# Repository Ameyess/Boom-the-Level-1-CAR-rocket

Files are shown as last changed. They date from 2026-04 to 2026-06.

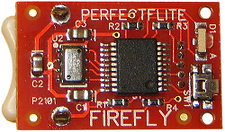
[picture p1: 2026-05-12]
Firefly/Firefly.png

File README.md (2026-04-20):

# Boom-the-Level-1-CAR-rocket
This is Boom (my level 1 certification rocket)

Boom is a single-stage Level 1 high-power rocket designed and built from scratch for CAR L1 certification. It features a 3D-printed nose cone, CNC-machined trapezoidal fins and a PerfectFlight Firefly altimeter for apogee detection as well as ejection charge deployment.

# Why I Built This
I've been fascinated by space and rockets since I was 10... playing games like Universe Sandbox and dreaming about what's out there beyond Earth. I loved learning how propulsion systems and aerodynamics work, seeing how to make things glide more smoothly through the air and how air can be a little funky. Since I was 10, I've been keeping up with this YouTuber called Integza and he really brought me into the world of rockets and propulsion. On top of all this I want to pursue a career in aerospace engineering. Instead of building a wind tunnel or a similar project, I wanted to get my L1 certification. I wanted to actually build something real before entering the field. Boom is that project: a fully designed, simulated, and flown (hopefully) rocket that I can point to and say I made it.

# Project images

## OpenRocket Design


## FULL CAD MODEL


## Nose Cone


## Body tube


## Fins


## Payload


## Link to Onshape
https://cad.onshape.com/documents/796e5f2c6edbdd94a10a7fd9/w/921c18dcc929cb2f28ee7e6d/e/6b2fc36c223bcd20e07954f4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

# Simulated Flight Performance 
To perform the simulations, I used OpenRocket. I first designed the whole rocket in OpenRocket then moved it to CAD for it to be fully 3D modelled and ready to construct. Simulations were run using the HP-H195NT-10 motor.

| Parameter | Value |
| --- | --- |
| Projected Apogee | 1484m | 
| Max Velocity | 470 m/s |
| Stability Margin| 1.8 Cal |
|Recovery | Parachute deployed at apogee|

# Design Overview
## Airframe
- Nose cone: 3D printed in PLA and includes an integrated altimeter bay in the shoulder
- Body tube: 18in long with a diameter of 1.325in
- Fins: Trapezoidal profile, CNC-machined from polycarbonate and chamfered to a knife's edge

## Recovery System
- Single parachute ejected at apogee
- Ejection charge triggered by PerfectFlight Firefly altimeter

## Avionics
- Altimeter: PerfectFlight Firefly: handles apogee detection and ejection charge deployment
- Mounted inside a dedicated compartment in the nose cone shoulder

## Motor
- Motor: Aerotech H135W-14A (or HP-H195NT-10 for simulation)
- Motor retained with a retaining ring (3d Printed)
- Rail lugs for launch rail guidance

## Graphs and Data



# BILL OF MATERIALS

| # | Name | Purpose | Qty | Total Cost (USD) | Distributor | Link |
|---|---|---|---|---|---|---|
| 1 | PLA Tough Plus | Printing the nose cone and various fins and parts of the rocket | 1 | $19.38 | Bambu Lab | [Link](https://ca.store.bambulab.com/products/pla-tough-upgrade?id=659539854443044866) |
| 2 | Aerotech Motor | Propulsion system for my L1 rocket | 1 | $44.63 | allrockets | [Link](https://www.allrockets.ca/High-Power-Rocketry/DMS/29/H195) |
| 3 | Parachute | Recovery system for the L1 rocket | 1 | $6.31 | allrockets | [Link](https://www.allrockets.ca/Build/Parachutes/Plastic-24) |
| 4 | Body Tube | The body tube for the L1 rocket | 1 | $2.51 | allrockets | [Link](https://www.allrockets.ca/Build/Airframes/55) |
| 5 | PerfectFlight Firefly Altimeter | Apogee detection and ejection charge deployment | 1 | $34.95 | PerfectFlite Direct | [Link](https://www.perfectflitedirect.com/) |
| 6 | Eye Bolts | Shock cord attachment | 2 | $7.06 | Apogee Rockets | [Link](https://www.apogeerockets.com/Building_Supplies/Misc_Hardware/Eyebolts_with_Washers_and_Nuts) |
| 7 | C-Tough Epoxy 125ml | Fin and bay attachment | 1 | $21.70 | allrockets | [Link](https://www.allrockets.ca/Build/Glue/C-Tough) |

_Note: The Eyebolts and the C-Tough Epoxy 125ml are already owned._

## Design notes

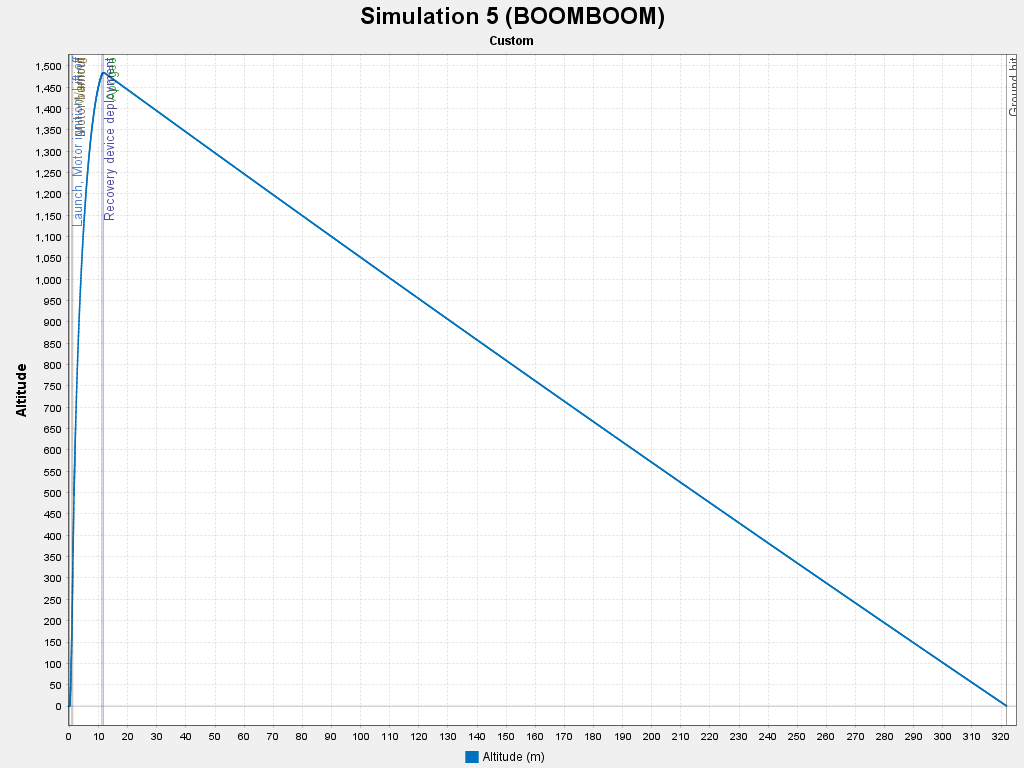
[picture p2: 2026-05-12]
BoomBoom_Sim/BoomBoom_altitude.png

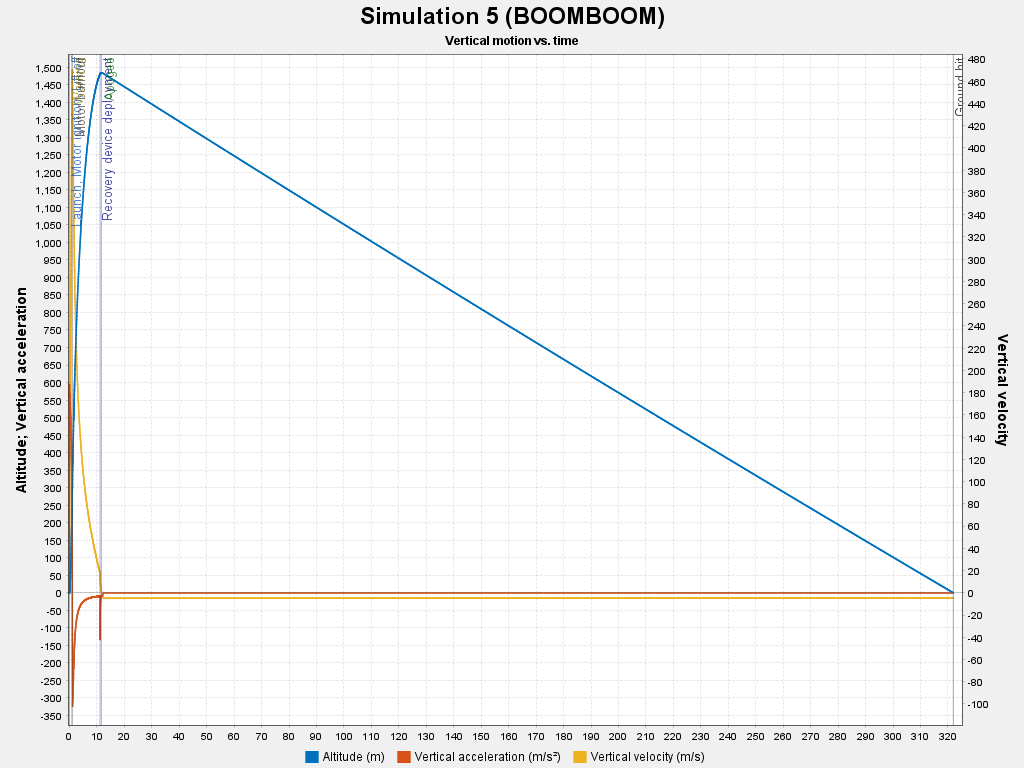
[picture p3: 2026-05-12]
BoomBoom_Sim/BoomBoom_Sim5_Motion_vs_Time.png

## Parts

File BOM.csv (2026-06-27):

Name | Purpose | Quantity | Total Cost (USD) | Link | Distributor
PLA Tough Plus | Printing the nose cone and various fins and parts of the rocket. | 1 | 19.38 | https://ca.store.bambulab.com/products/pla-tough-upgrade?id=659539854443044866 | Bambu Lab
Aeroteck motor | Propulsion system for my L1 rocket | 1 | 44.63 | https://www.allrockets.ca/High-Power-Rocketry/DMS/29/H195 | allrockets
Parachute | Recovery system for the L1 rocket | 1 | 6.31 | https://www.allrockets.ca/Build/Parachutes/Plastic-24 | allrockets
Body tube | The body tube for the L1 rocket | 1 | 2.51 | https://www.allrockets.ca/Build/Airframes/55 | allrockets

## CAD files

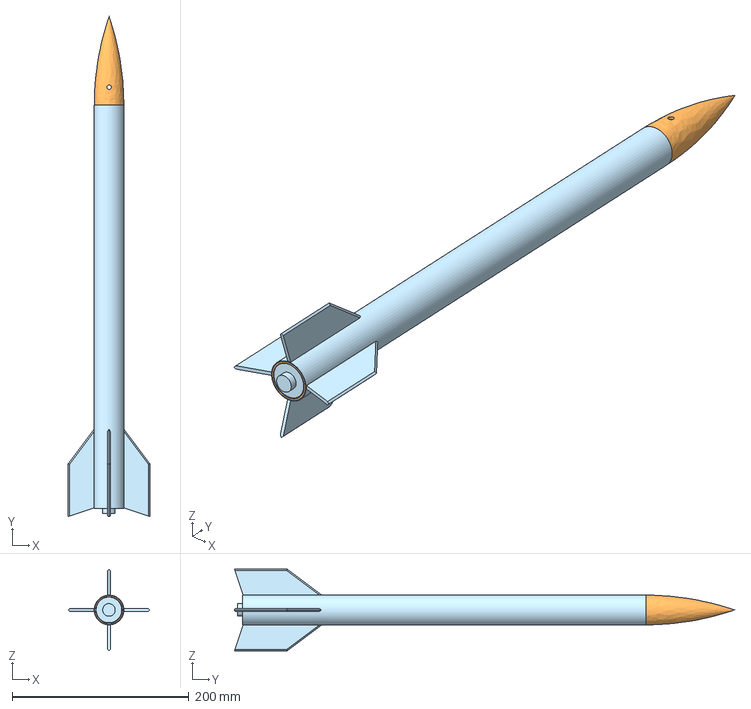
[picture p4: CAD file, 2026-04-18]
CAD_BoomBoom/Boom Final Assembly.step
92.4 x 566.1 x 92.4 mm

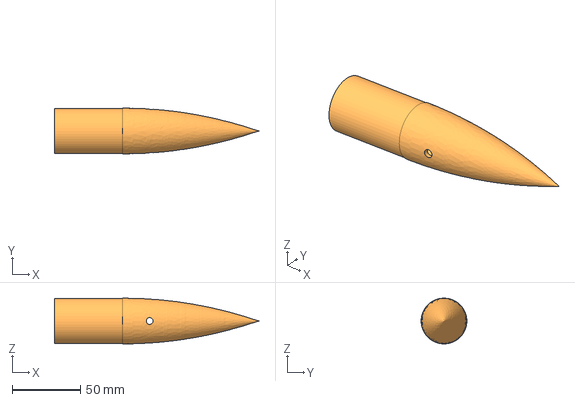
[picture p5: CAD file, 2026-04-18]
CAD_BoomBoom/Nosecone.step
150.0 x 33.7 x 33.7 mm

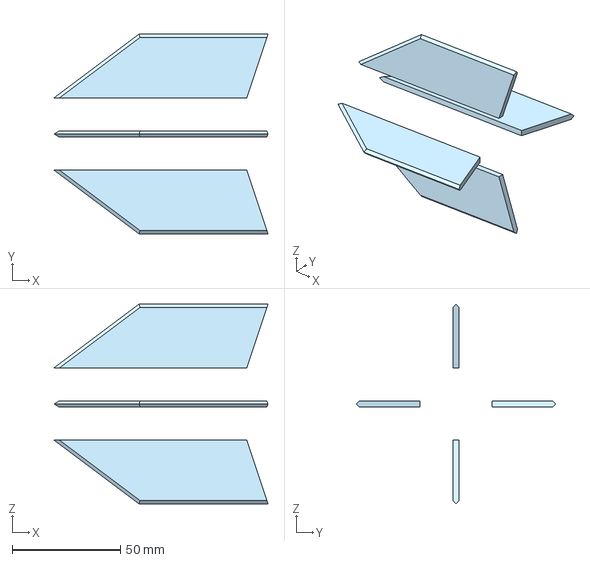
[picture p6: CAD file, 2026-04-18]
CAD_BoomBoom/fin (1).step
99.0 x 92.4 x 92.4 mm

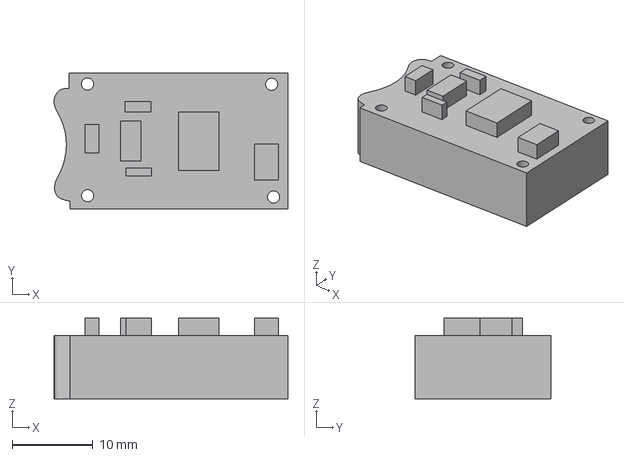
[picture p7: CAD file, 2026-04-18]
CAD_BoomBoom/Firefly.step
28.9 x 16.8 x 10.0 mm

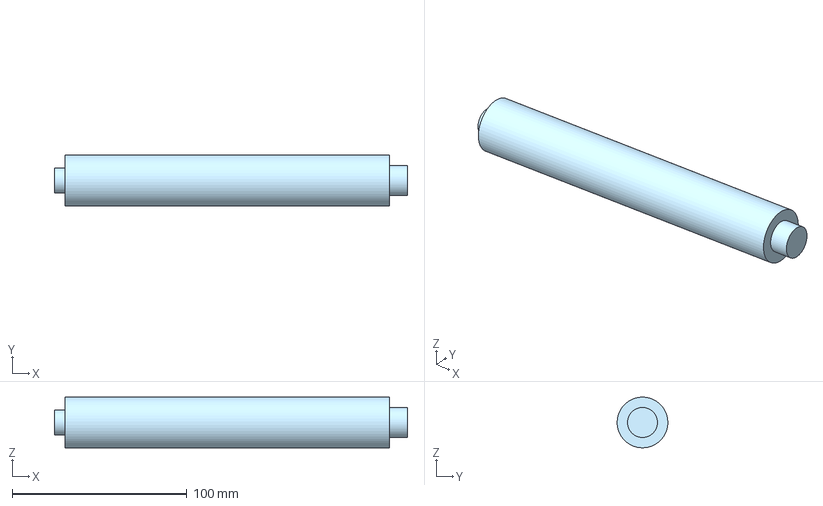
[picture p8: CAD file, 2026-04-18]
CAD_BoomBoom/Rocket Motor.step
201.8 x 29.0 x 29.0 mm

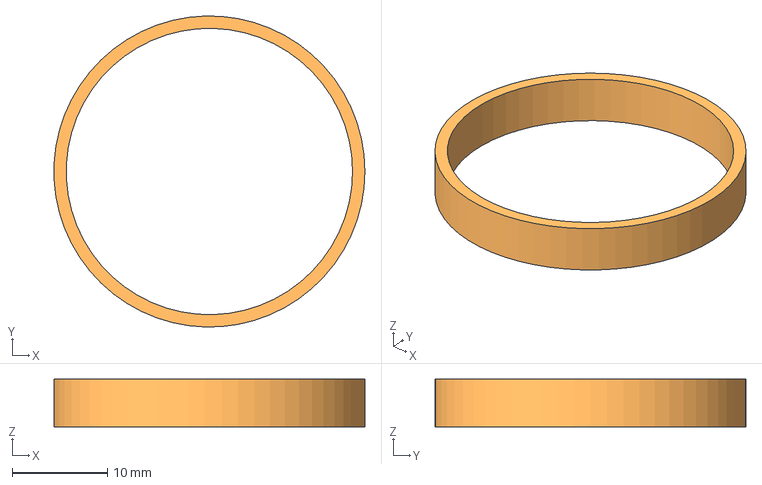
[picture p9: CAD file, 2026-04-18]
CAD_BoomBoom/Centring Rings.step
32.6 x 32.6 x 5.00 mm

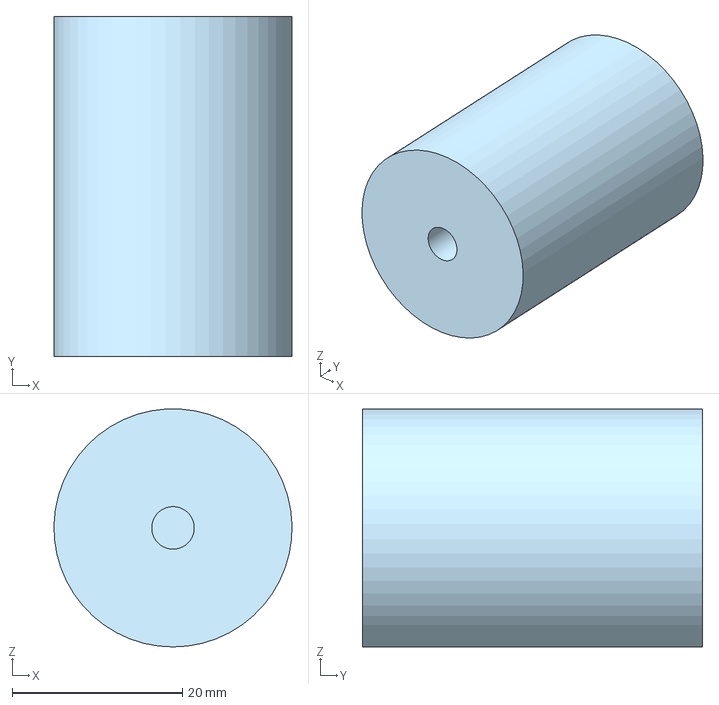
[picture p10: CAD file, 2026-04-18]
CAD_BoomBoom/Payload.step
28.0 x 40.0 x 28.0 mm

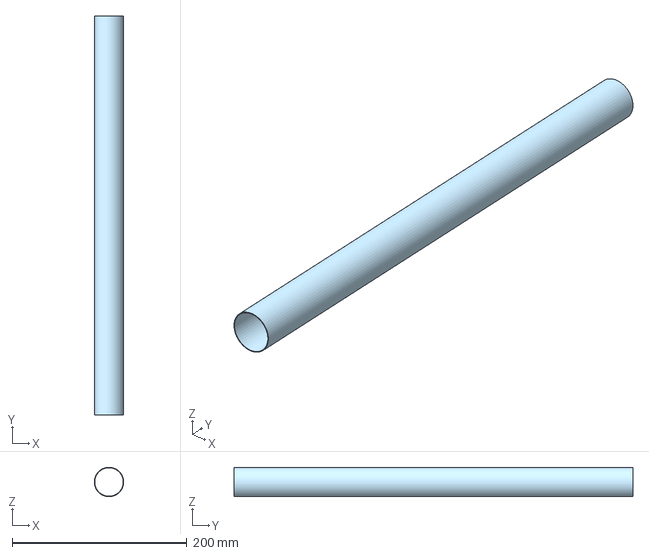
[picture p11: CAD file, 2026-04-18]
CAD_BoomBoom/Body Tube.step
33.7 x 457.0 x 33.7 mm

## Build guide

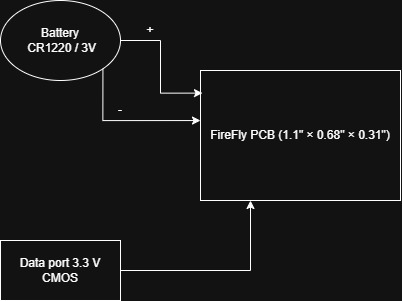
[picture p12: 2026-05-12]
Firefly/Firefly Wiring Diagram.jpg

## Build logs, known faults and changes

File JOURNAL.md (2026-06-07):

---
title: "Boom Boom - L1 Rocket"
author: "your-name"
description: "Building and certifying an L1 high-power rocket called Boom Boom, including CAD, simulations, avionics, and launch prep."
created_at: "2026-04-05"
---

# April 5: Worked on the initial design of the rocket

Made good progress on the L1 rocket project today. Got the rough CAD model built out in OpenRocket with all the main components sorted out: nose cone, body tube, trapezoidal fins, parachute, shock cord, and engine block. Also ran the motor simulations with the HP-H195NT-10, and the numbers are looking good. Projected apogee is around 1,482 m, max velocity of 471 m/s (Mach 1.389), and stability margin is at 1.8 cal, which is right where it should be for a L1 rocket. Additionally, the recovery deployment looks clean at apogee. I'm happy with how the development is going, and the next step will be refining the CAD and ordering parts.

OpenRocket simulation

OpenRocket simulation 2

OpenRocket simulation 3

**Total time spent: 2 hours**

# April 6: Worked on refining the L1 Rocket and researching parts

Today I looked at some example L1 rockets and found that the motor requires a retaining ring. This ring holds the motor in place during launch and prevents it from ejecting out of the rocket. I also came across a few ways to 3D print this part instead of buying it, which I might do since it's the cheaper option.

I also spent time working on my Onshape document and adding components. One of the bigger frustrations today was trying to track down a 3D model of the motor I want to use (H135W-14A). There just aren't any available online, so I had to move on from that for now.

From there, I shifted focus toward designing a payload bay that can sit inside the nosecone and house an altimeter and GPS unit. I put together a rough model of the frame. The top two compartments will hold the altimeter and GPS equipment, and the middle sections will hold a battery or whatever other payload ends up being needed.

Overall, today was mainly design work again, but more focused on refining exactly what the rocket needs to include. Next session, I'm aiming to get the motor added into the CAD and update the masses in OpenRocket.

Payload bay CAD

Payload bay CAD 2

**Total time spent: 1 hour**

# April 7: Worked on adding more details to the CAD and researching parts

Today I worked on the payload portion of Boom, the L1 rocket. This session was a mix of both CAD and research for various components and parts of the rocket. However, there are still uncertainties to solve.

On the research side, I landed on a GPS solution: the Pocket-GPS design using a GPS Neo-6M module paired with an ESP32. This should allow for a cheap and reliable GPS solution. It can display altitude, latitude, longitude, speed, and satellite count, which covers everything needed to track the rocket. I need to research how to send the information back to a server to track the rocket's position.

I also started sizing out the payload bay compartments around these components and looked into mounting and fastener options for securing everything inside the bay. The main roadblock was the uncertainty around specific dimensions and specs of the fasteners and parts. Without the exact measurements of the GPS modules, most of the modeling still feels like an estimate until those numbers are confirmed.

Next session, I will confirm the physical specs of the GPS and ESP32 modules and get them properly modeled into the CAD.

CAD payload bay

CAD payload bay 2

CAD payload bay 3

CAD payload bay 4

**Total time spent: 1.5 hours**

# April 8: Worked on CAD and Research

Today I continued working on the payload section of Boom, though this session ended up being more of a research detour than I had planned. Coming off of last journal, I had originally planned to confirm the physical specs of the GPS and ESP32 modules and get them properly modeled into the CAD, but that didn't happen.

Once I started pricing everything out, I realized the module would have cost way too much. The GPS Neo-6M and ESP32 combo seemed like a solid, cheap solution, but dedicated altimeter modules on top of that pushed the cost too high.

Instead of sticking with the ESP32 route, I started looking at alternatives. One strong option is a simple Arduino Nano paired with a BMP280 barometric pressure sensor, which reads altitude by detecting changes in atmospheric pressure. This has been proven by many other DIY rockets. The whole setup should cost around $20 USD, which wouldn't push the budget too far. This will cover altitude; however, I still need to figure out the GPS portion and how to log the data.

On the other side of the session, I shifted over to CAD and started working on the motor geometry. I found the official motor assembly drawing, which gave me the key dimensions I needed. Using that as a reference, I was able to model it out in CAD and create a rough outline of what the rocket engine might look like. I still want to double-check with real images and blueprints what the exact dimensions of the rocket motor are.

Next session, I want to compare the Arduino Nano and BMP280 option, look into any affordable GPS modules that are worth considering, as well as continuing the CAD now that the motor geometry is in a good place.

Motor CAD

Motor CAD 2

Motor CAD 3

Motor CAD 4

**Total time spent: 2 hours**

# April 9: Worked on MORE CAD, Avionics, and shtuff :)

Today I continued working on Boom, and just like last session, I ran into a few problems.

Today's goal was to compare the Arduino Nano and BMP280 option, look into affordable GPS modules, and keep adding detail to the CAD. The CAD part happened, but the electronics took a turn for the worse.

I realized the Arduino Nano and BMP280 combo I had been considering doesn't actually work out. So I went back to square one on the avionics side and started looking at what other DIY and L1 rocketeers are actually using. Two options stood out to me the most: the Eggtimer ION and the PerfectFlight Firefly. The Firefly is cheaper, but it won't give me as much data as the Eggtimer.

I also did a check for the L1 requirements. Parachute recovery is mandatory for good certification because I have already incorporated a parachute into Boom. However, I still need to find out the right ejection charge delay so the parachute opens at or after apogee.

On the CAD side, I got the motor geometry dialled in, and the engine now fits properly within the airframe. The assembly is starting to look like an actual rocket. I also added the rail lugs and the centering rings for the motor.

Next session: make a final call on the altimeter — ION vs. Firefly.

CAD assembly

CAD assembly 2

CAD assembly 3

CAD assembly 4

CAD assembly 5

**Total time spent: 2 hours**

# April 10: Worked on avionics and CAD

Today I continued working on Boom and decided on the altimeter debate from last session. The goal of this session was to finalize the altimeter module and then add and modify the CAD to accommodate it.

I went with the PerfectFlight Firefly over the Eggtimer ION. The lower cost and smaller form factor are better for an L1 flight. Additionally, it is better to keep the L1 flight simple, so fewer things can go wrong. The Firefly handles apogee detection and ejection charge deployment, which is everything I need for a certification flight.

On the CAD side, I designed a small compartment for the payload bay to house the Firefly. It sits within the nose cone shoulder and will be glued to hold it in.

Overall, this session was pretty good. I finalized the altimeter, and the next session will be focusing on finalizing the CAD and submitting the design for review.

Firefly compartment CAD

Firefly compartment CAD 2

**Total time spent: 1 hour**

# April 12 (2 AM): Worked on CAD

Today's session on Boom was a CAD-focused one. The main tasks were tidying up the existing components, chamfering the edges of the fins, and assigning materials and weights to the parts. It is important to get these items filled out before running simulations, as mass and aerodynamics do play a role in the overall performance of the rocket. I also modeled a few miscellaneous bits and pieces that hadn't been addressed yet, such as the eye bolts. I also added the pilot holes for the altimeter.

Today's session went on without a hassle and was smooth. Next session should be the final push to wrap up the CAD and get the design ready for review.

CAD fin detail

CAD assembly

CAD fin chamfer

**Total time spent: 0.5 hours**

# April 12 (10 AM): Final touches

Today I worked on the final touches for Boom. There was not much to CAD or research, so I spent some time exploring possible decals and logos for the rocket. Apart from that, I also worked on some miscellaneous things, such as fixing the assembly and addressing other minor issues.

Overall, I am happy with how the design turned out, and I think it will fly great and hopefully reach the speeds I am aiming for. I also sliced the nose cone and fins, so they are ready to print. For the fins, I created a technical drawing so they can be sent to the CNC machine at my robotics team.

I really like this logo, as it is minimalistic yet detailed enough to look great. I think the rocket would look awesome flying with it.

Rocket decal

Logo option 1

Logo option 2

**Total time spent: 0.5 hours**

# May 3: Final touches Mk2

In this session, I worked on updating the model to incorporate the feedback from the review. I went through each point raised and worked on getting the necessary updates done. I also uploaded the BOM as a CSV file to GitHub, which had been flagged as missing.

I also took the time to talk with several experienced L1 rocket flyers to get some real-world answers to the review concerns. For the question of how the rocket will be controlled and guided, they explained that with a properly stable rocket, the thrust pushes downward and the rocket moves in the opposite direction thanks to Newton's Third Law. On top of this, the rocket will also be guided on a launch rail during ignition to keep it upright while the motor gets up to speed.

For the visibility side of it, many people recommended making the rocket a very bright colour so it stays visible to the naked eye as it descends, as a tracker is way out of the budget, as shown in previous journals.

Review feedback

**Total time spent: 1 hour**

# May 7: Final touches Mk3

**Questions to Answer**

**a)** If you can't do trajectory control, how are you going to make sure it's not going anywhere it's not supposed to be?

**b)** How will the Firefly be retrieved if you don't know where it is?

**c)** How are you going to make sure the thing isn't going to go down barrelling at terminal velocity and destroying itself?

**Responses**

**A)** For the question of how the rocket will be controlled and kept on course without trajectory control, the answer comes down to stability and launch setup. As stated in a previous journal, in a properly stable rocket, the thrust pushes downward, and the rocket moves in the opposite direction. This might raise concerns because even the most stable rockets do drift and can change direction, which is why I included fins in my rocket design. The fins will help the rocket stay in the air while maintaining its stability. Additionally, RocketPy simulations accurately show where the rocket will end up.

RocketPy simulation — red line is the rocket flight path

**B)** In addition to simulating and predicting where the rocket will land, we will paint it a bright colour so it remains visible to the naked eye as it descends.

**C)** For the concern about the rocket coming down at terminal velocity and destroying itself, this is handled through the recovery system. The rocket will have a parachute already listed in the parts list, along with an ejection charge built into the motor itself. When the motor burns out, the charge fires automatically, and users can adjust the time by using the provided tool in the rocket motor package, as well as an alternative tool which I already own.

**Use of the Firefly**

The onboard Firefly computer will only be used to track altitude during the launch. The Firefly does not have a GPS, a way to detach the chute, or any other function within the rocket. Since the Firefly acts as its own module, I could not find/make a wiring diagram for it.

I hope these answers clarify where Boom Boom is heading, and I hope now you guys can see my vision. :)

**Total time spent: 1 hour**

# May 12: Final touches Mk4

In today's session (final session before build, hopefully), I worked on the reviewers' feedback.

Reviewer feedback

**Point 1 — GitHub Organizing**

The first part of the feedback that caught my eye was the horrendous-looking GitHub; I 100% agree that it should be organized into folders. In this session, I did just that: I organized the GitHub into folders for CAD, Simulations, and the Firefly payload altimeter module.

The CAD folder houses the CAD for BoomBoom.

CAD folder

The Simulation folder holds the various simulations I did on trajectory and stability.

Simulations folder

The Firefly folder holds the manual for my altimeter module as well as the wiring diagram for it.

Firefly folder

Firefly folder 2

**Point 2 — Stability Without Movable Fins**

The second piece of feedback was a concern about how the rocket would remain stable and on course without active trajectory control or movable fins. This was a major concern of mine when I was designing the rocket; however, I have since learned that active stabilization is not necessary for a safe flight.

Boom Boom uses fixed fins, not movable ones, and that is completely normal. Fixed fins are the standard for amateur and high-power rocketry at this scale. The fins provide stability by shifting the Center of Pressure (CP) rearward, below the Center of Gravity (CG). As long as the CG is above the CP by at least one calibre (one body diameter), the rocket is considered stable. When the rocket pitches or tilts even slightly, the airflow hits the fixed fins and generates a strong opposing force that pushes the tail back into alignment with the rest of the rocket, keeping it flying straight up.

This has been verified in OpenRocket and confirmed through the RocketPy simulations shown in previous journal entries. The simulations account for wind, drift, and real-world flight conditions to accurately predict where Boom Boom might end up.

To summarize, the fins on Boom Boom do not move; however, if the rocket pitches or tilts, the resulting aerodynamic force acting on the fins will push the tail back to compensate, restoring stable flight.

**Total time spent: 1.5 hours**

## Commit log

2026-04-12 Added all files that needed to be 3D printed in STEP format
    [Assembly 1 (1).step, Centring Rings.step, Nosecone.step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]
2026-04-18 Enhance README with project details and images
    Expanded the README with detailed project information, including design overview, simulated flight performance, and bill of materials.
2026-06-27 Rename L1 - Rocket - Boom Boom-bom (1).csv to BOM.csv
    [BOM.csv]
